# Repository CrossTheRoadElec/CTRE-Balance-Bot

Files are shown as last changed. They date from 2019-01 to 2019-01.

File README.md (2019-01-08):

# CTRE Balance Bot v2

## What's In Here
- STL files for printing the balance bot: **[CAD Files](CAD/)**
- Instructions on how to assemble the balance bot: **[Builders Guide](Documentation/)**
- Source code to get the balance bot balancing on its own

## What You Need
- 3D Printer or means of printing the required STL files
- Phoenix NETMF v5.1.5.0 (Found in Phoenix 5.6.0.0 found [here](http://www.ctr-electronics.com/installer-archive))
- The Balance Bot Kit sold from CTR Electronics at http://www.ctr-electronics.com/

## What This Is

Balance Bot

This is a demo robot that shows how PID can be used to control something inherently unstable (an inverted pendulum) in a very controllable manner.

This is done through various control schemes, that you can look at [here](#control-schemes)

## How To Make One
1. Assemble the hardware as shown in the **[Builders Guide](Documentation/)**.
2. Ensure Phoenix 5.6.0.0 is installed and Phoenix NETMF 5.1.5.0 is referenced in the solution explorer.

http://www.ctr-electronics.com/installer-archive

This can be confirmed below...

Assembly Version Reference

3. Flash all hardware using Phoenix Lifeboat.
    1. HERO firmware is 1.2.0.0
    2. Talon firmware is 11.8
    3. Pigeon firmware is 0.41
4. Deploy code to HERO.
5. Done!

## Controls
All the controls are configurable within the source code, you can change any button you want.
Default controls are:
- A - Re-Zero the balance bot to make its current pitch the 0 pitch
- X - Enable closed-loop control of the balance bot to attempt to balance on the surface
- Start - Enable *Pixy Control* mode
- Shift from D input to X input mode - Disable robot
- Shift from X input to D input mode - Enable robot
---
Gain Tuning Controls:
- RB - Increment currently selected gain by increment amount shown in yellow above gains
- LB - Decrement currently selected gain by increment amount shown in yellow above gains
- Back - Cycle increment amount between 0.001 -> 0.010 -> 0.100 -> 1.000 -> 10.00 -> 0.001
- B - Cycle currently selected gains by P -> I -> D -> P
- Y - Cycle currently selected gains by Top -> Mid -> Bottom -> Top

## Control Schemes
There are also various features available that allow for better control

- Cascaded PID Loop
  - (Pixy Camera PID) feeds desired velocity to maintain distance into a
  - Velocity Control PID feeds angle to maintain velocity into a 
  - Balance Control PID outputs percent output to maintain angle
  - The outer control loop (Velocity) runs at a slower rate than the inner loop (Balance) to ensure the balance loop has time to react to any velocity changes. This is key to ensuring the robot balances properly.
- Fall Detection
  - When the robot surpasses a specified angle for too long, it will have *tipped over*.
  - When *tipped over*, the robot must be uprighted for some time before it will be given control again and attempt to balance again.
  - The *tipped over* angle changes based on the velocity of the robot, if it's moving forward a great velocity, it is unable to accelerate in that direction for very much, so the fall detection recognizes it is unable to recover if angled in the direction of travel and determines it has *tipped over*
    - Likewise, if the robot is moving forward at a great velocity, it is able to angle against the direction of travel at a greater angle than normal due to it having more room to accelerate without having it *tipped over*.
 - Pixy Camera
    - Every robot has the ability to enable *Pixy Control* mode by pressing start on the gamepad.
    - *Pixy Control* is visible due to the screen having turned blue on the robot
    - If the robot has a Pixy Camera attached to it, it will actively look for blue objects with a similar luninence to the Display Module Screen
        - If it finds an object that matches what it's looking for, it will take control away from the user and attempt to face in its direction and maintain a distance such that the height of the target matches a predefined height in the code.
    - If there is no Pixy Camera attached to a robot with *Pixy Control* active, it will just have the blue screen on and have full user control, other robots will still be able to follow it.
- Low Battery Voltage Detection
    - Once the battery is measuerd to be less than what the robot expects a battery voltage to be at (currently set to 11.00V), the robot will enter *Low Battery* mode.
    - While in *Low Battery* mode, the robot will feel sluggish and the display will show a red background if not in *Pixy Control* mode.
    - Once the robot is in *Low Battery* mode, it will not exit until the voltage reaches a good voltage (currently 11.50V). This is to ensure the robot does switch between *Low Battery* and good battery due to motor loads.
    - This feature is to ensure the battery does not discharge below a certain point, and to let the user know the battery is low so they can charge it.

## What's the screen for?
The screen is used for debugging purposes, when dialing in gains it's useful to be able to change the gains on the fly to test various gains without having to re deploy the application.

It also displays the current pitch the robot is at, along with the battery voltage it is measuring, whether closed looping is enabled or not, and what the percent output to the motors are at. All of this is useful for debugging various issues with the robot.

Lastly, there are points on the screen, normally 'o's. They show what direction each wheel of the robot is traveling in. This is useful as it allows the builder to double check they did the wiring correctly. If the robot is pushed forward such that the wheels turn, both of the displays should show up as a '+'. If just one wheel is pushed forward, only that side should show up as a '+'. Likewise for going backwards, they should show up as a '|' or when viewed directly at it a '-'.

Besides this, it will turn blue when the robot is in *Pixy Control* mode, this allows other pixy cameras to detetct where the robot is and attempt to face towards the blue-screened robot and maintain a distance away from the robot.

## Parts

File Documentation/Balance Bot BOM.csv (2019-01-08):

Subteam | Part | Part Number | Quantity | Link | Details
Drivetrain(pololu) | 30:1 37D metal gearmotor | 2823 | 2 | https://www.pololu.com/product/2823
 | 6mm D hub | 1083 | 1 | https://www.pololu.com/product/1083 | 2 - pack
 | 6mm D hub (alt) | RB-Sct-1045 | 2 | https://www.robotshop.com/en/6mm-clamping-d-hub-tapped-0770-pattern.html
 | Traction Tire | 217-2859 | 1 | https://www.vexrobotics.com/vexpro/motion/wheels-and-hubs/traction-wheels.html | 2 - pack
Control System | Talon SRX | 14-838288 | 2 | http://www.ctr-electronics.com/talon-srx.html
 | HERO Dev board | 16-728279 | 1 | http://www.ctr-electronics.com/hro.html
 | Pigeon IMU | 16-737785 | 1 | http://www.ctr-electronics.com/gadgeteer-imu-module-pigeon.html
 | Display Module | 16-688380 | 1 | http://www.ctr-electronics.com/gadgeteer-display-module.html | Cable Included
 | CAN Connector | 15-676778 | 1 | http://www.ctr-electronics.com/can-connector-5-pack.html
 | Ribbon Cable | 14-886867 | 1 | http://www.ctr-electronics.com/talon-srx-data-cable-4-pack.html
 | Power Breakout PCB | 17-806679 | 1 | http://www.ctr-electronics.com/power-distribution-breakout.html
 | Talon SRX Encoder Breakout Board | 15-696679 | 2 | http://www.ctr-electronics.com/talon-srx-encoder-breakout-board.html
 | Battery | 522-1009-ND | 1 | https://www.digikey.com/product-detail/en/b-b-battery/BP3-12-T1/522-1009-ND/653330
 | Battery Charger |  | 1 | https://www.amazon.com/Energizer-ENC2A-Battery-Charger-Maintainer/dp/B01GSI1S08?s=automotive
 | Velcro |  | 1 | https://www.amazon.com/Monoprice-Hook-Loop-Fastening-0-75-inch/dp/B004AF9II6
 | Fuse holder | 8110K4 | 1 | https://www.mcmaster.com/#8110k4/=1dkxrrj
 | Fuse | F4201-ND | 1 | https://www.digikey.com/product-detail/en/littelfuse-inc/0287020.PXCN/F4201-ND/2519821 | Same fuse as PDP hardware kit
 | Black Anderson housing | 17-808066 | 6 | http://www.ctr-electronics.com/anderson-power-pole-44.html | Battery to Power & Motors to Talons
 | Red Anderson housing | 17-808082 | 6 | http://www.ctr-electronics.com/anderson-power-pole.html | Battery to Power & Motors to Talons
 | Yellow Anderson housing | 17-808089 | 1 | http://www.ctr-electronics.com/anderson-power-pole-46.html | CAN Diagnostic port
 | Green Anderson housing | 17-808071 | 1 | http://www.ctr-electronics.com/anderson-power-pole-45.html | CAN Diagnostic port
 | PP15 crimp | 879-1332 | 6 | http://www.ctr-electronics.com/anderson-power-pole-contact-42.html | Motor Power & CAN port
 | PP45 crimp | 879-261G2 | 8 | http://www.ctr-electronics.com/anderson-power-pole-contact-43.html | Talons & Battery & Power
 | 12AWG silicon wire RED | 15-838782 | 5 | http://www.ctr-electronics.com/red-silicone-wire-12-awg.html
 | 12AWG silicon wire BLACK | 15-838766 | 5 | http://www.ctr-electronics.com/black-silcone-wire-12-awg.html
 | Orange 20 awg furrle | 15-705048 | 1 | http://www.ctr-electronics.com/ferrule-20-awg.html
 | White 18 awg furrle | 15-704956 | 1 | http://www.ctr-electronics.com/ferrule-18-awg.html
 | USB A to mini male B | 16-856566 | 1 | http://www.ctr-electronics.com/usb-a-male-b-mini-cable.html
 | USB A to A | 16-856565 | 1 | http://www.ctr-electronics.com/usb-a-male-cable.html
Hardware | 4-40 .25"(1/4) legnth SH | 92196A106 | 1 | https://www.mcmaster.com/#92196a106/=1dlje7x | 10 Total
 | 4-40 .5"(1/2) length SH | 92196A110 | 1 | https://www.mcmaster.com/#92196a110/=1dljeei | 70 Total
 | 4-40 nylock hex nut | 91831A005 | 1 | https://www.mcmaster.com/#91831a005/=1dljdbn | 28 Total
 | #4 washer | 92141A005 | 1 | https://www.mcmaster.com/#92141a005/=1dlkrwv | 30 Total
 | 8-32 1" length | 92196A199 | 1 | https://www.mcmaster.com/#92196a199/=1dljfxc | 4 Total
 | M3 6mm length SH | 91502A102 | 1 | https://www.mcmaster.com/#91502a102/=1dljgex | 12 Total
Tools | #43 Drill | 2901A217 | 1 | https://www.mcmaster.com/#2901a217/=1dytp8s
 | 1/8" Drill | 2901A115 | 1 | https://www.mcmaster.com/#2901a115/=1dytt2i
 | #25 Drill | 2901A198 | 1 | https://www.mcmaster.com/#2901a198/=1dytth4
 | 4-40 Tap | 2522A665 | 1 | https://www.mcmaster.com/#2522a665/=1dytw9t
 | Locktite | 1004A12 | 1 | https://www.mcmaster.com/#1004a12/=1e2fvdl

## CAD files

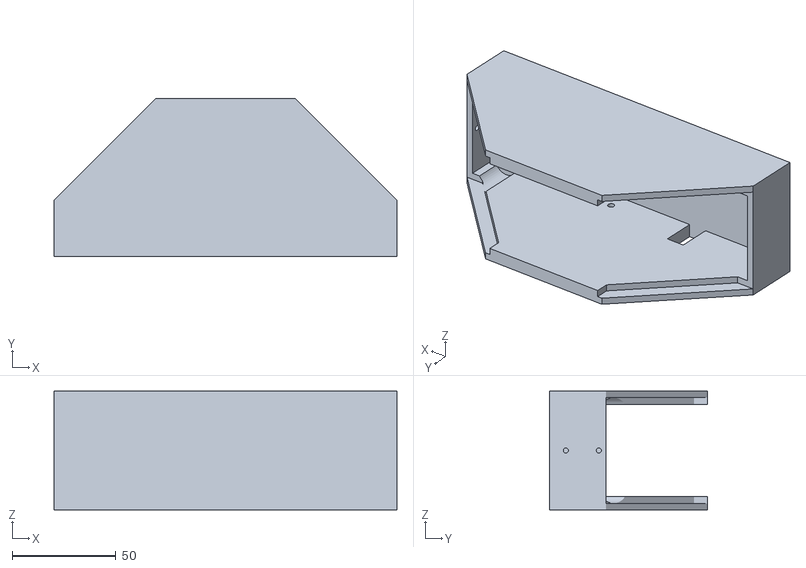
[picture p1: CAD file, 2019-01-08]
CAD/Dock Assm - Dock Corner-1.STL
165.1 x 76.2 x 57.1

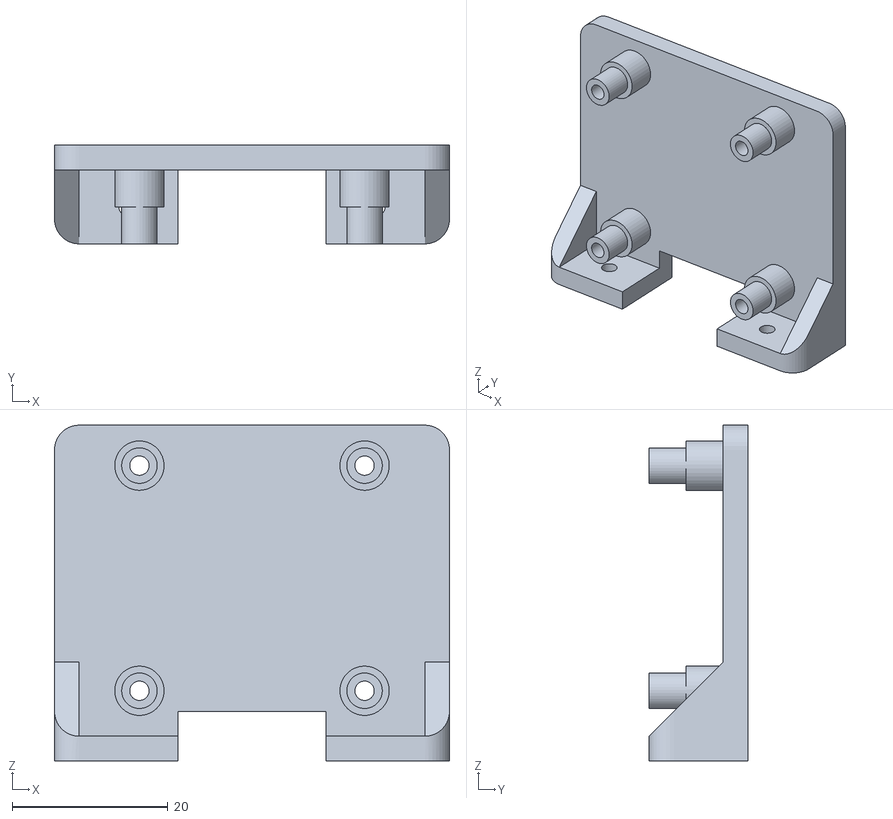
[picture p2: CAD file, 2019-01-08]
CAD/Pigeon Mount.STL
50.8 x 12.7 x 43.2

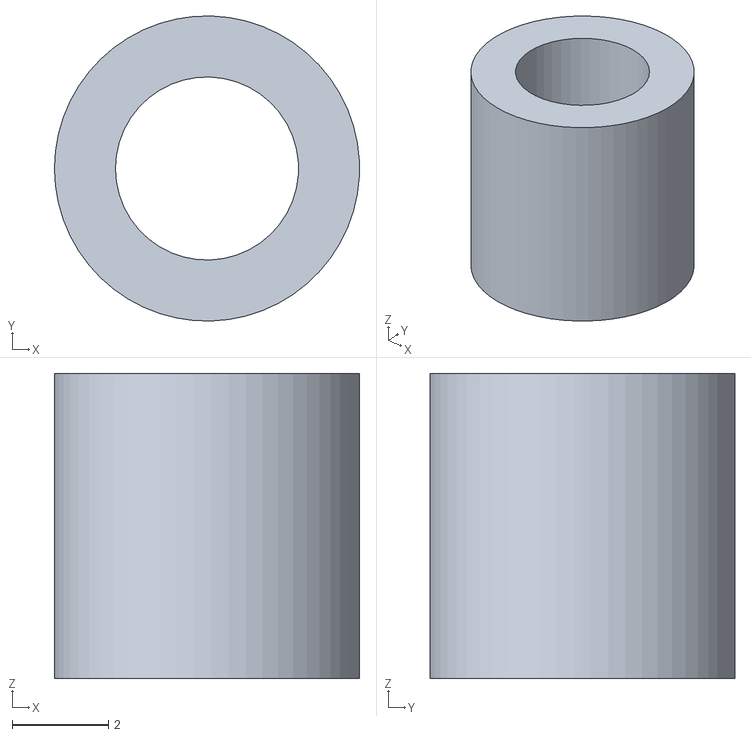
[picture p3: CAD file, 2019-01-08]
CAD/Spacer.STL
6.35 x 6.35 x 6.35

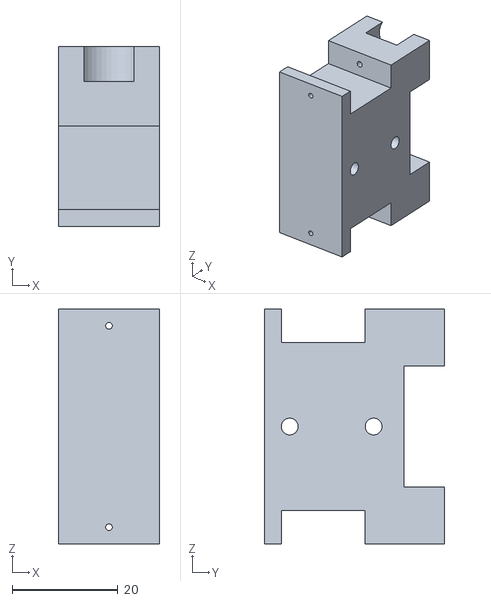
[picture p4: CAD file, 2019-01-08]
CAD/Dock Assm - Pogo Clamp-1.STL
19.1 x 34.0 x 44.4

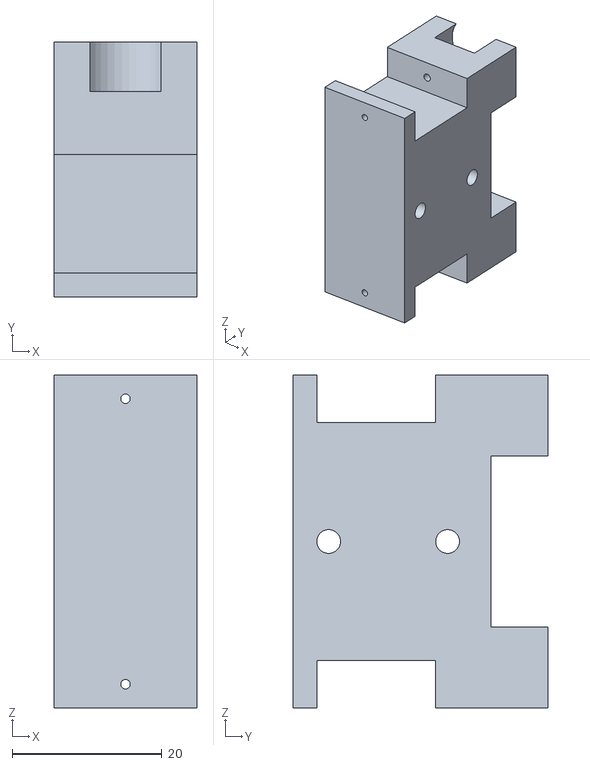
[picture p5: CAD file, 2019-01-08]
CAD/Pogo Clamp.STL
19.1 x 34.0 x 44.5

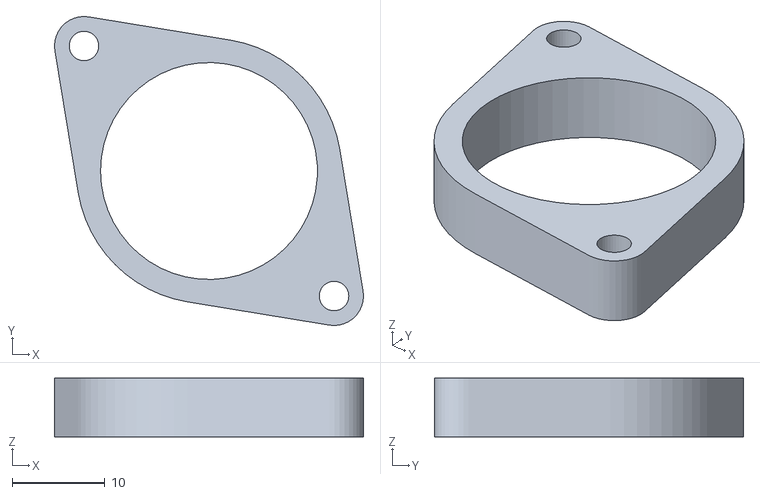
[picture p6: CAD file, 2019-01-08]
CAD/Switch Cover.STL
33.3 x 33.3 x 6.35

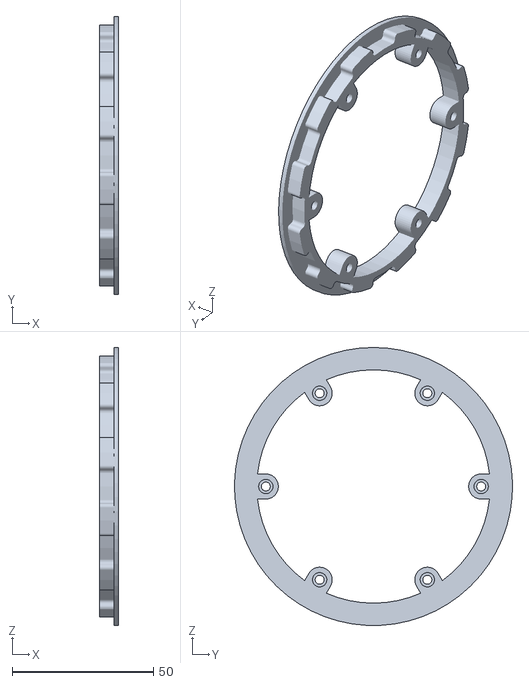
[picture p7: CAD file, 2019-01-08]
CAD/4in Traction flange.STL
6.67 x 98.4 x 98.4

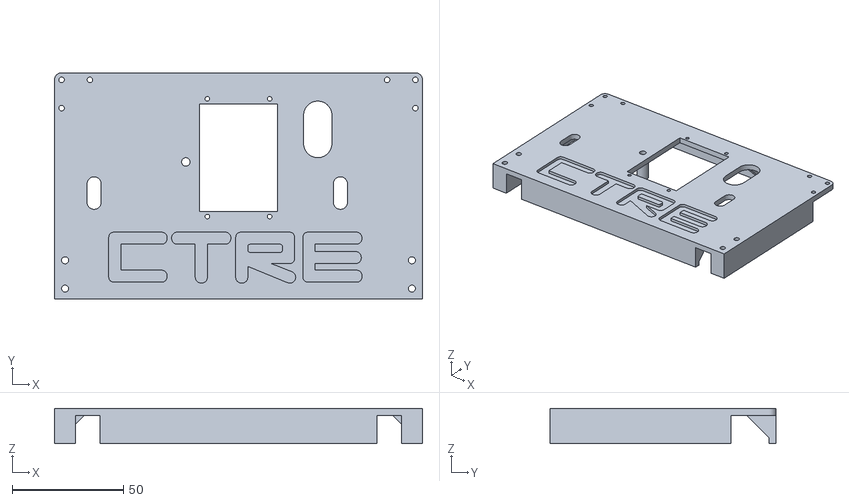
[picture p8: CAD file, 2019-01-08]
CAD/Front Cover V2.STL
165.1 x 101.6 x 15.9

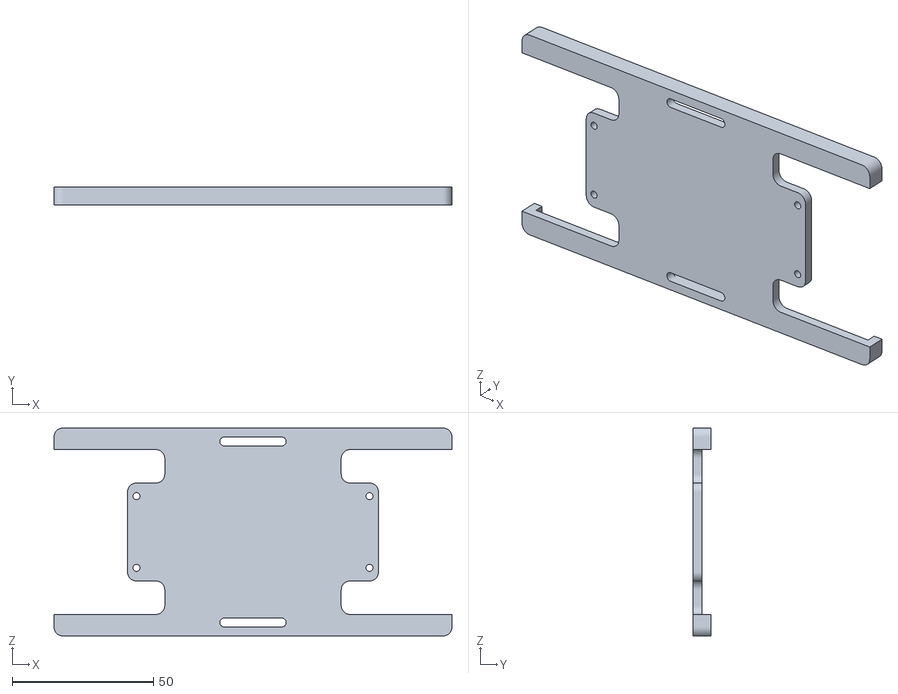
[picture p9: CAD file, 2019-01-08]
CAD/Cross beam.STL
141.0 x 6.35 x 73.7

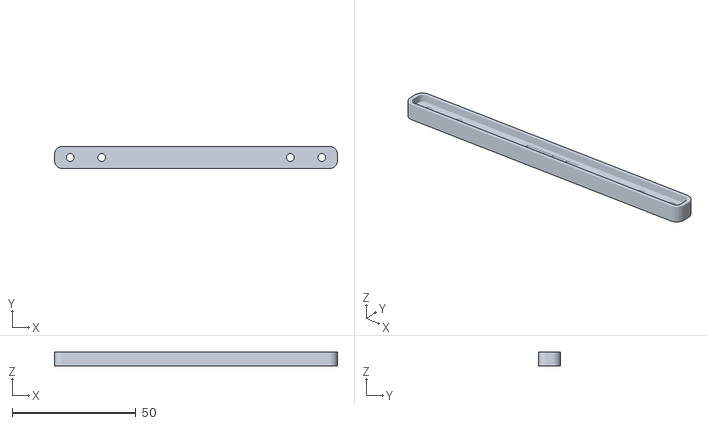
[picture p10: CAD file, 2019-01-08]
CAD/Front Support.STL
114.3 x 8.89 x 5.72

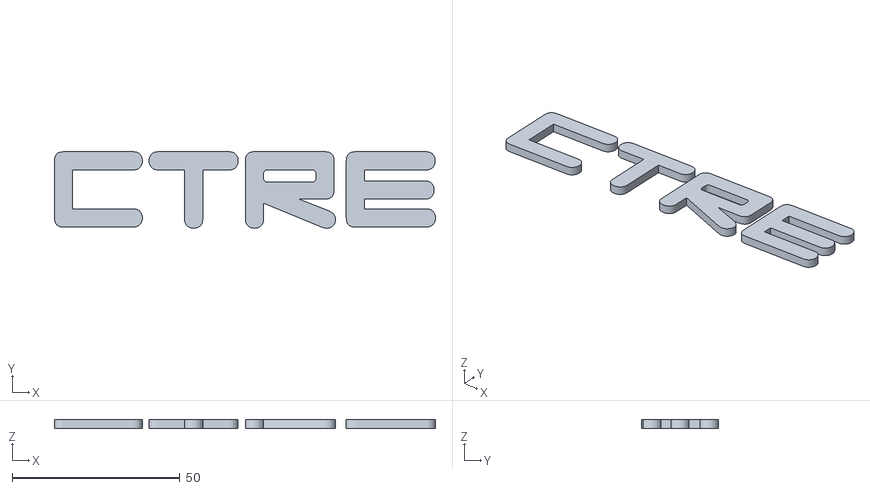
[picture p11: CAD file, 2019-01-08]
CAD/CTRE lettering.STL
113.7 x 22.9 x 2.54

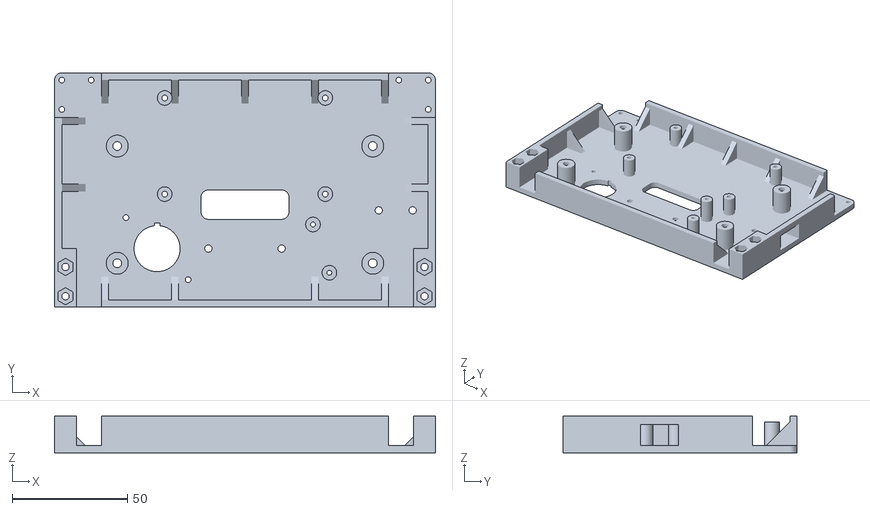
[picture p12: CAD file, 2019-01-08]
CAD/Back Cover V2.STL
165.1 x 101.6 x 15.9

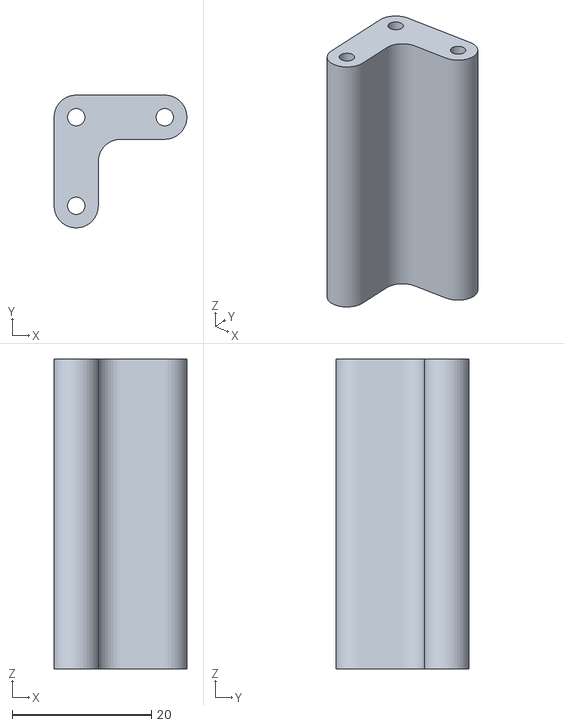
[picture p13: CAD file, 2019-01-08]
CAD/Corner Support.STL
19.1 x 19.1 x 44.5

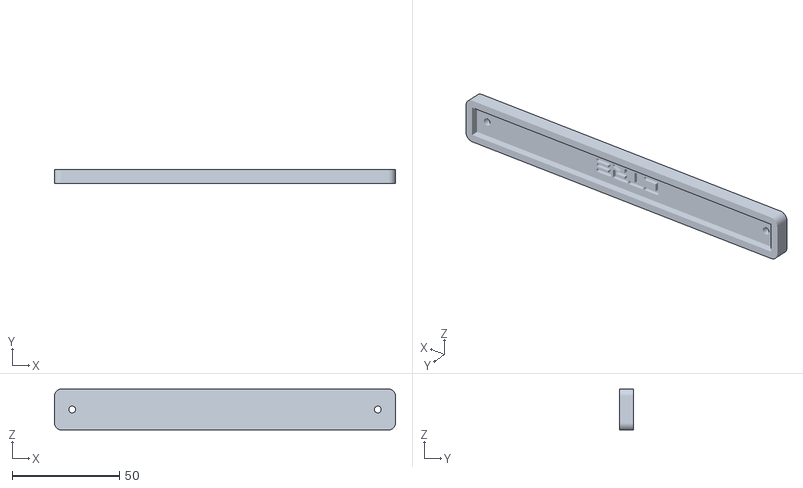
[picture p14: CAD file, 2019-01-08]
CAD/Bottom Support.STL
158.8 x 6.35 x 19.1

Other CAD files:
CAD/CTRE 4in Traction flange.STL
CAD/Dock Corner.STL
CAD/Side Support.STL
CAD/4in Traction hub V2.STL
CAD/4in Traction hub.STL
CAD/Motor mount.STL

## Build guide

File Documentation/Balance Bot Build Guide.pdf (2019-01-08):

# Balance Bot Build Guide

## Table of Contents

# Introduction

Purpose: To provide an economic robotic platform that utilizes many CTRE control system products for programming entertainment, while being cheap and easy to manufacture with just a 3D printer and hand tools.

Port layout:

- USB Mini is accessible from the top of the robot.

Tools:
- Drill Bits
- #43 (#4 Tap)
- ⅛ (#4 through hole)
- #25 (#8 tap)
- Allen wrenches (recommended : Harbor Freight (https://www.harborfreight.com/10-Pc-SAE-T-Handle-Hex-Key-Set-62161.html) )
- 3/32 (#4 socket head bolt)
- 9/64 (#8 Socket head bolt)
- Needle Nose Pliers
- Electrical
- Wire strippers
- Ferrule Crimper (http://www.ctr-electronics.com/weidmuller-ferrule-crimper.html)
- Anderson Crimper (http://www.ctr-electronics.com/anderson-powerpole-crimper-crimp.html)
- Snips
Material:
- .9lbs PLA Filament

# Printing Parts

## 1. Print a Back Cover

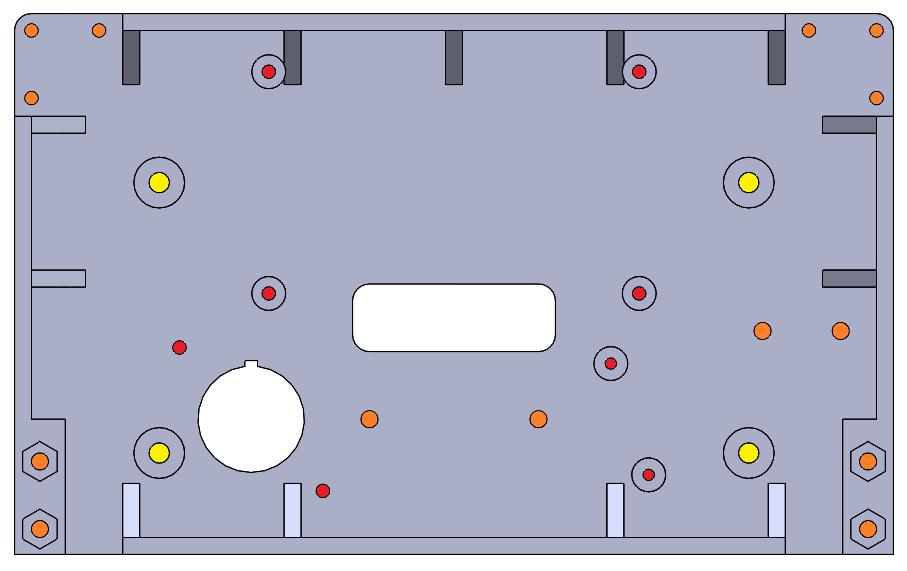
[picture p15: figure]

a. Drill RED holes with #43 drill
b. Drill ORANGE holes with ⅛ drill
c. Drill YELLOW holes with #25 drill

d. Press #4 lock nuts into hex

## 2. Print a Front Cover

a. Drill RED holes with #43 drill

b. Drill ORANGE holes with ⅛ drill
c. Drill YELLOW holes with #25 drill

## 3. Press in #4 Nuts into hex grove

*make sure the nylon on the nut is facing the correct direction

## 4. Print two Motor Mounts

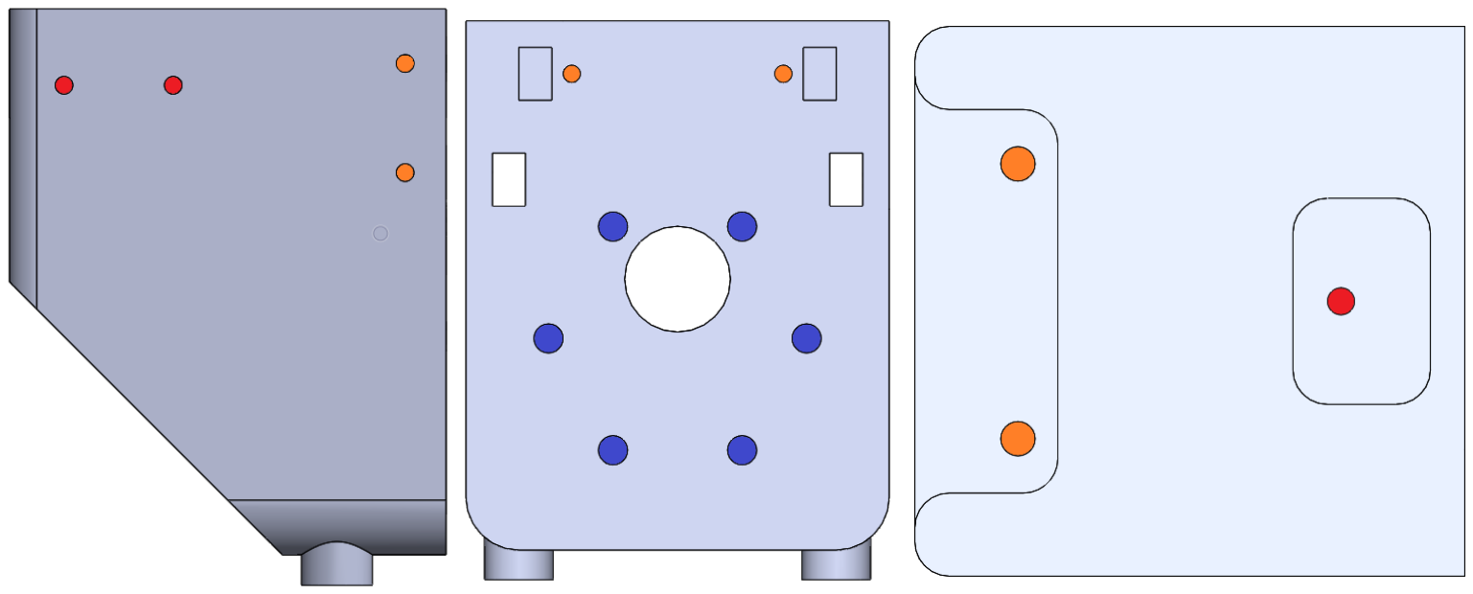
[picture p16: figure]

a. Drill RED holes with #43 drill
b. Drill ORANGE holes with ⅛ drill
c. Blue holes are for M4 bolts

## 5. Print two Side Supports

a. Drill out ORANGE holes with ⅛ drill

## 6. Print a Cross Beam

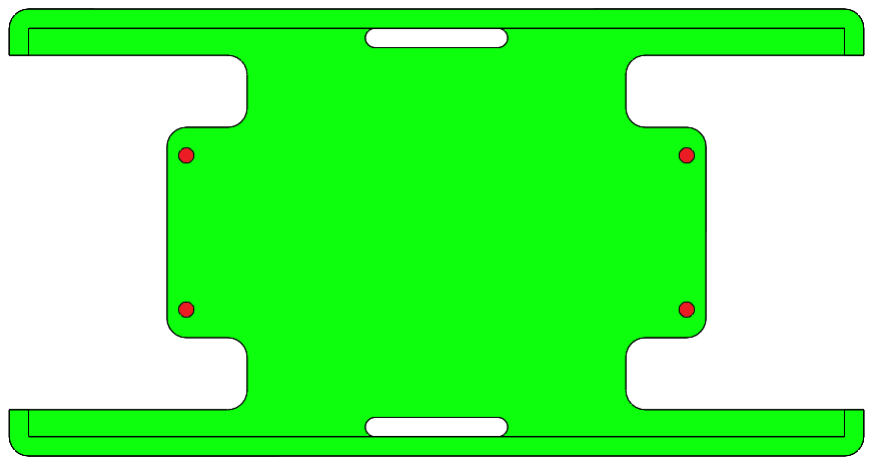
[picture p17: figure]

a. Drill RED holes with a #43 drill

## 7. Print a Pigeon Mount

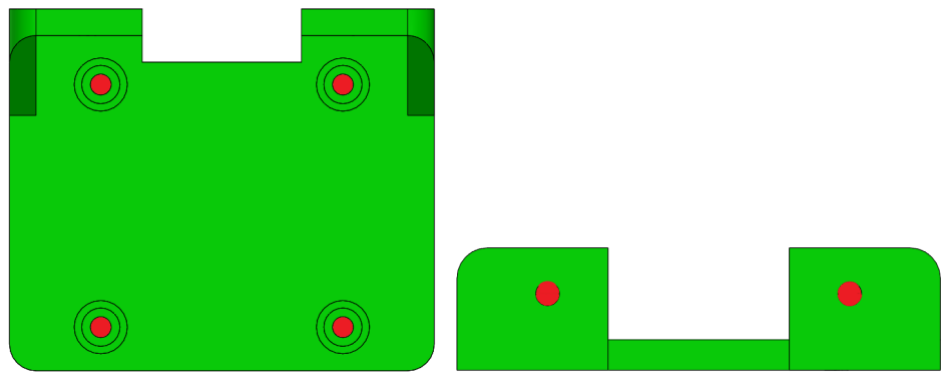
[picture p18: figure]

a. Drill RED holes with #43 drill

## 8. Print two Corner Supports

a. Drill RED holes with a #43 drill on both sides

## 9. Print two Front Supports

a. Drill ORANGE holes with ⅛ drill

## 10. Print two 4in Traction Hub

a. Drill ORANGE holes with ⅛ drill

b. Press in #4 nuts into hex groove

## 11. Print two 4in Traction Flange

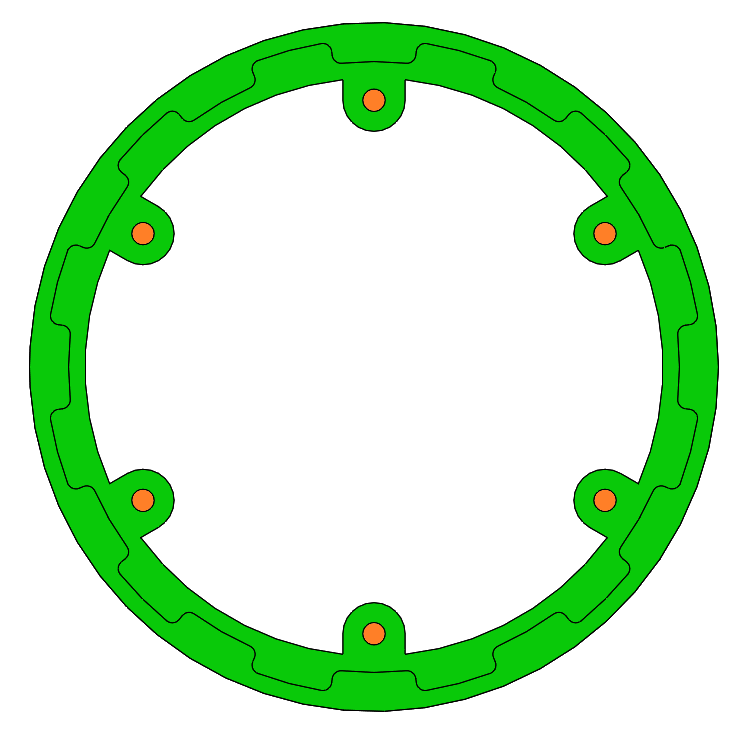
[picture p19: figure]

a. Drill ORANGE holes with ⅛ drill

## 12. Print four spacer

# Assembly

## 1. Assemble Wheel

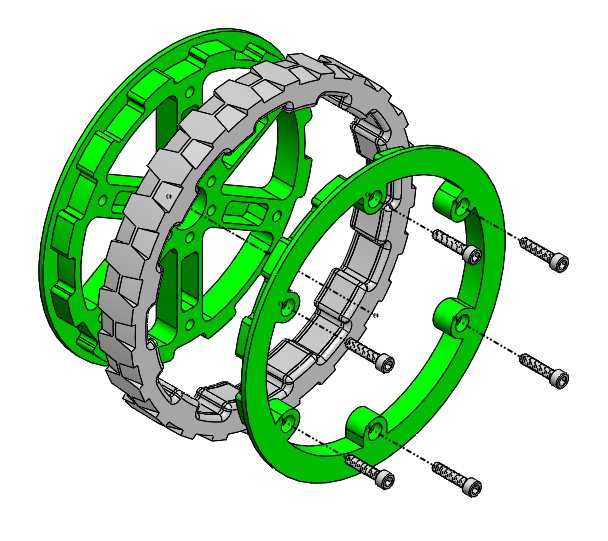
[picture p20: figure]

a. Sandwich the Traction wheel between the Hub and Flange, Secure with .5” 4-40 bolts

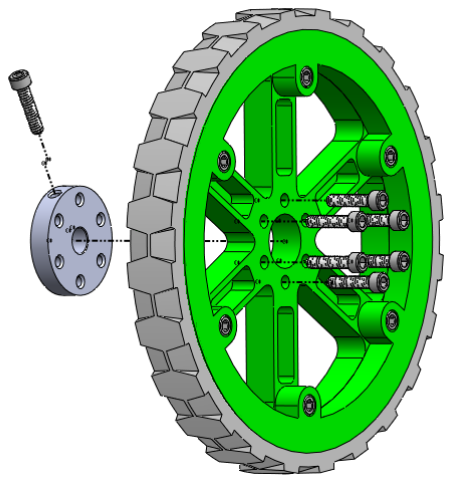
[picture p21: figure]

b. Attach the Pololu Mounting Hub to the Hub using .5” 4-40 bolts
c. Insert an additional .5” 4-40 into the Pololu Mount Hub to use as a set screw

## 2. Assemble Lower Frame

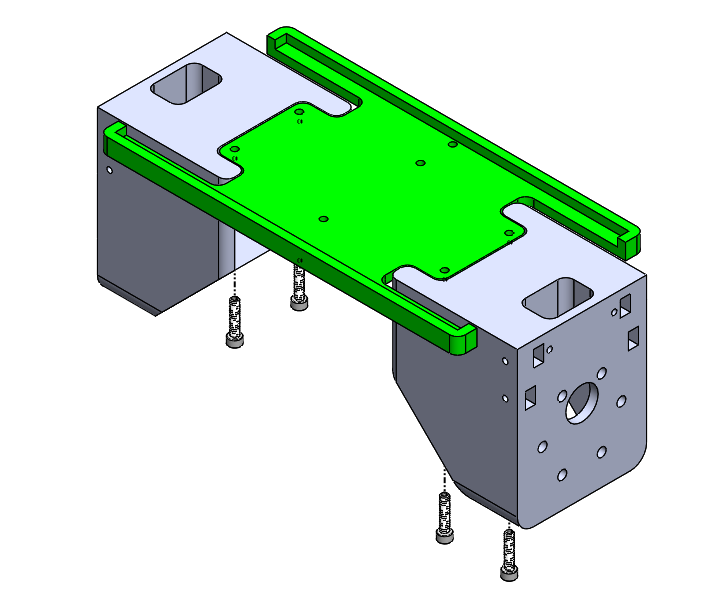
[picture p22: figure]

a. Attach the Motor Mounts to the Cross Beam using .5” 4-40 bolts

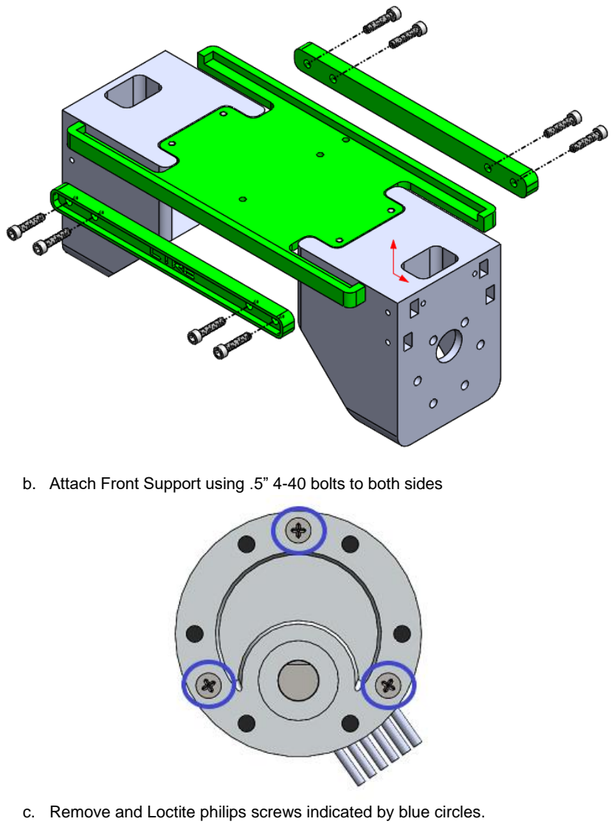
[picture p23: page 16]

b. Attach Front Support using .5” 4-40 bolts to both sides
c. Remove and Loctite philips screws indicated by blue circles.

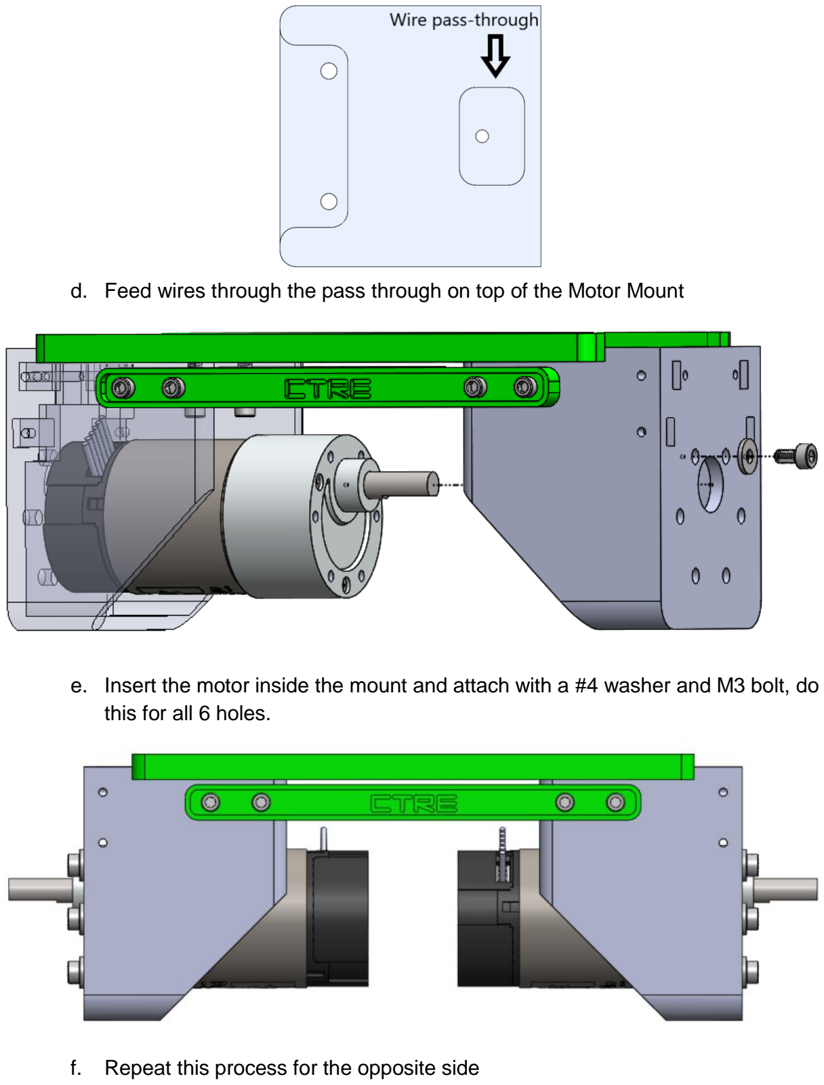
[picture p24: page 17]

d. Feed wires through the pass through on top of the Motor Mount
e. Insert the motor inside the mount and attach with a #4 washer and M3 bolt, do this for all 6 holes.
f. Repeat this process for the opposite side

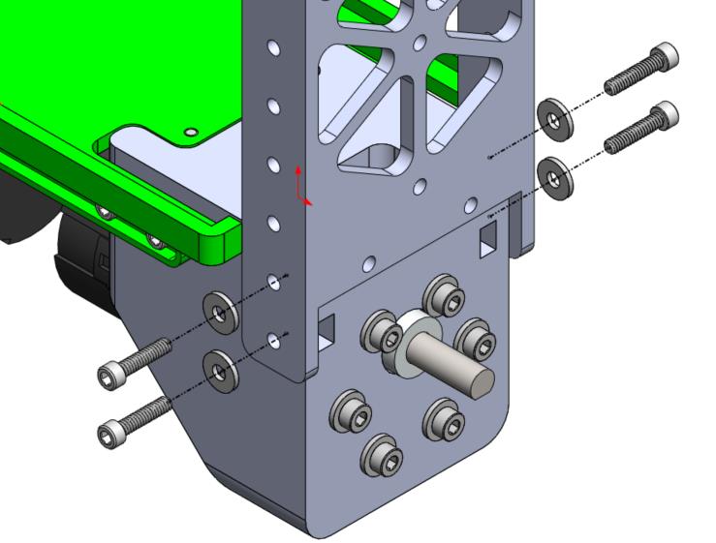
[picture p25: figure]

g. Attach the Side Supports using #4 washers and .5” 4-40 bolts(with nuts already installed)

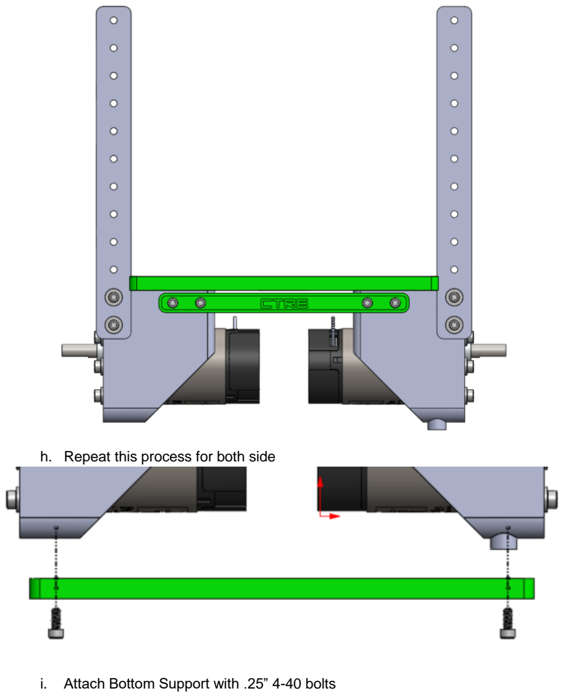
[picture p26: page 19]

h. Repeat this process for both side
i. Attach Bottom Support with .25” 4-40 bolts

## 3. Assemble Back Cover

a. Attach Corner Support with .5” 4-40 bolts Wire Electronics
Power Wiring Diagram

# Signal Wiring Diagram

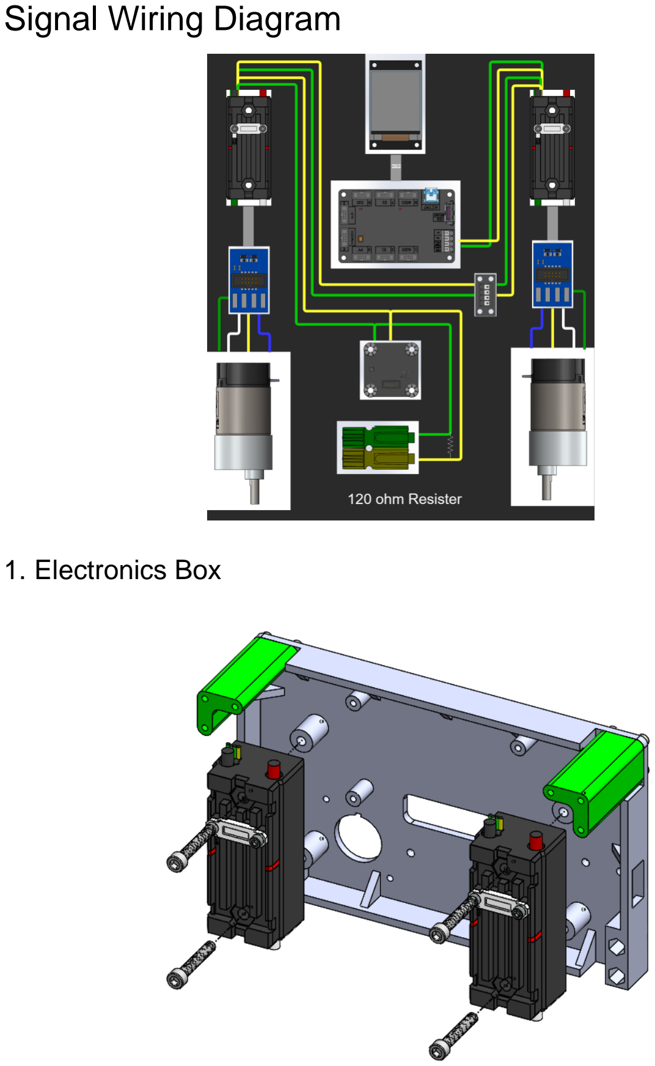
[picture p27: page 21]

## 1. Electronics Box

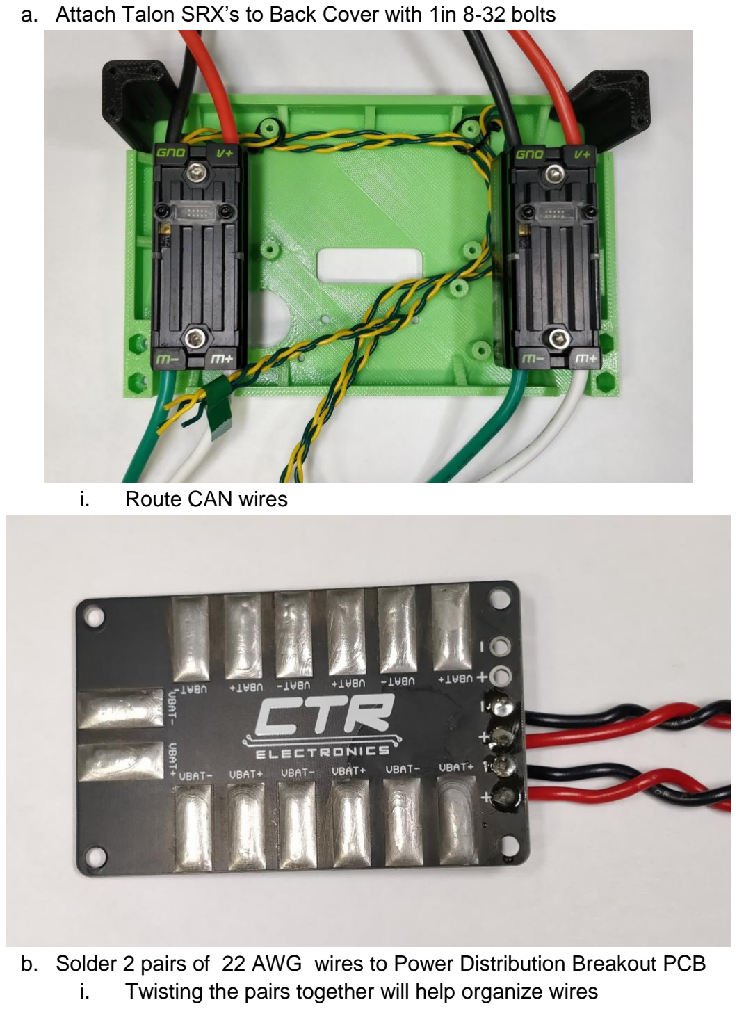
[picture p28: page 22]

a. Attach Talon SRX’s to Back Cover with 1in 8-32 bolts
i. Route CAN wires
b. Solder 2 pairs of 22 AWG wires to Power Distribution Breakout PCB
i. Twisting the pairs together will help organize wires

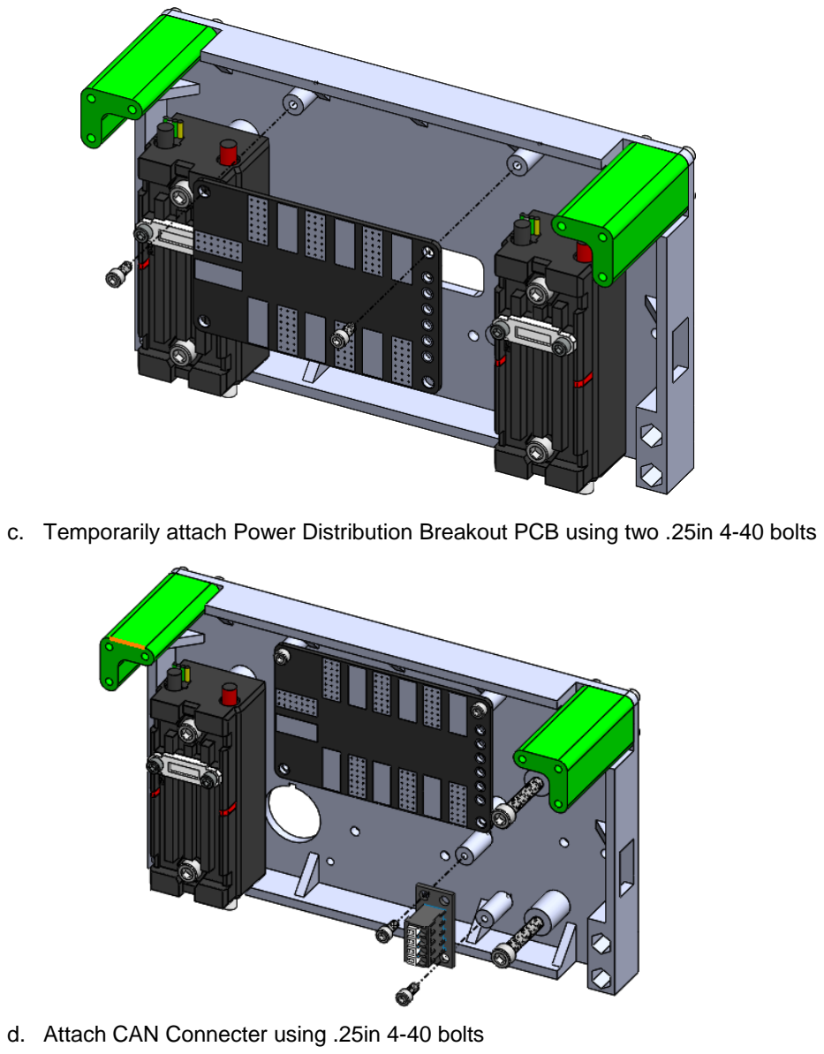
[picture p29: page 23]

c. Temporarily attach Power Distribution Breakout PCB using two .25in 4-40 bolts
d. Attach CAN Connecter using .25in 4-40 bolts

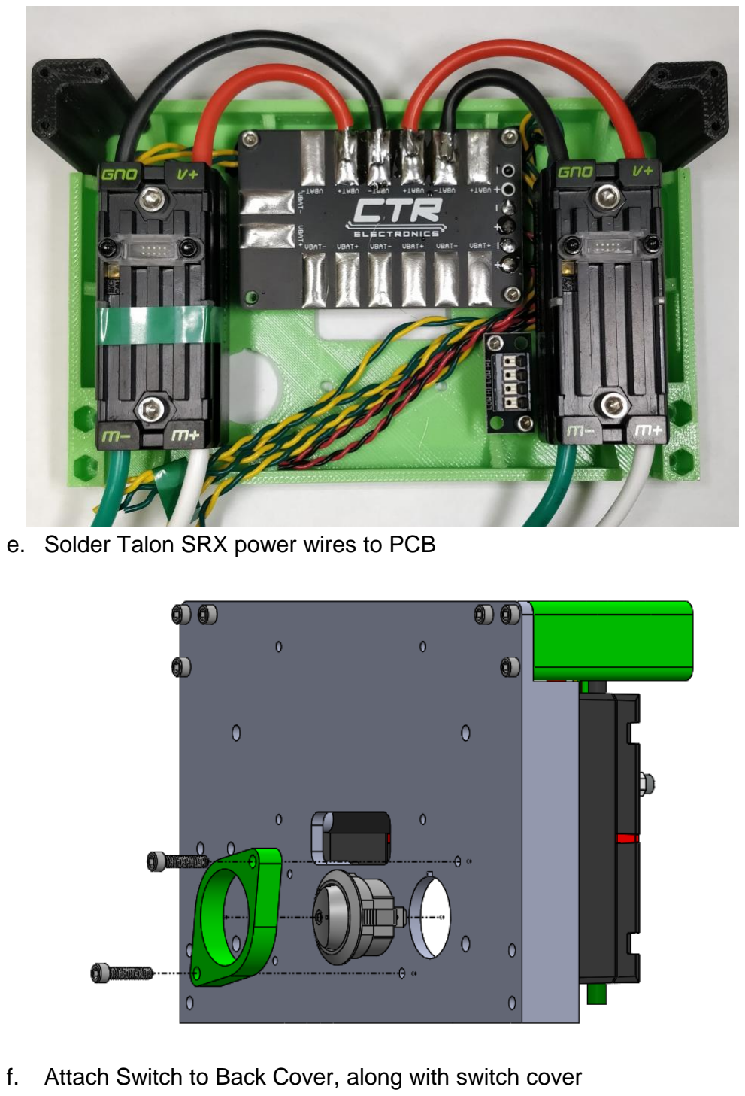
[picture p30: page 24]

e. Solder Talon SRX power wires to PCB
f. Attach Switch to Back Cover, along with switch cover

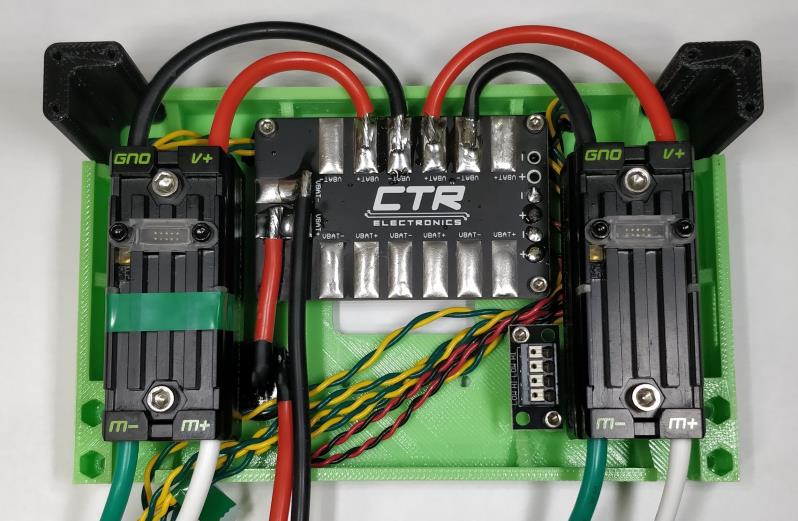
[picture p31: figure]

g. Solder 12 AWG wire from the Switch to the PCB and route battery cable and attach Andersons
h. Take out the two temporary .25in 4-40 bolts

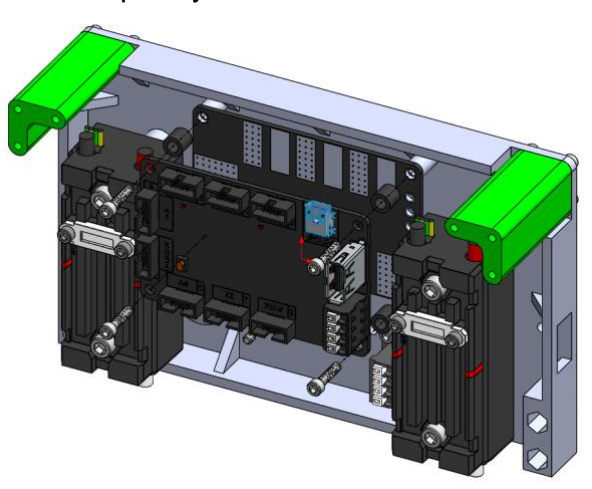
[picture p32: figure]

i. Attach the HERO Development board using .5in Spacers and .5in 4-40 bolt
j. Use Ferrules to plug in CAN to HERO and CAN Connector. Along with with Power to HERO

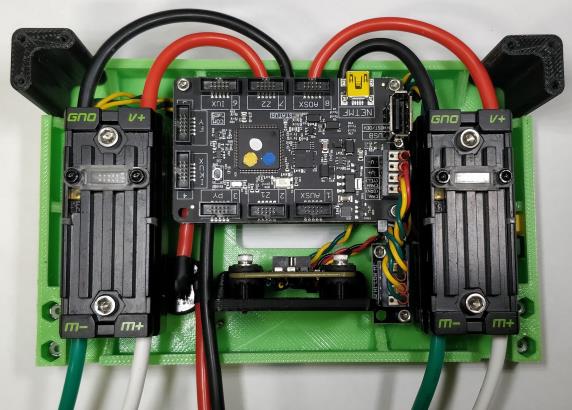
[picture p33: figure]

k. Solder power and CAN wires to Pigeon and mount Pigeon

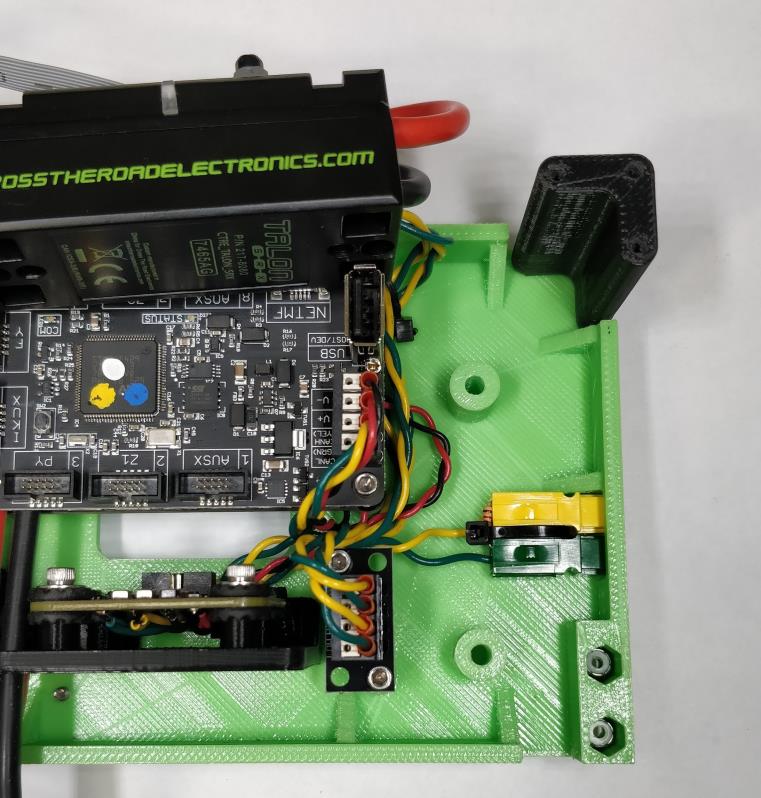
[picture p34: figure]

l. Anderson CAN
i. Optional 120 Ohm resistor with Anderson

# Final Assembly

## 1. Assemble Upper frame

a. Attach Display to Front Cover with .25in 4-40 bolts
i. Plug in display module using a 4in Gadgeteer Data Cable

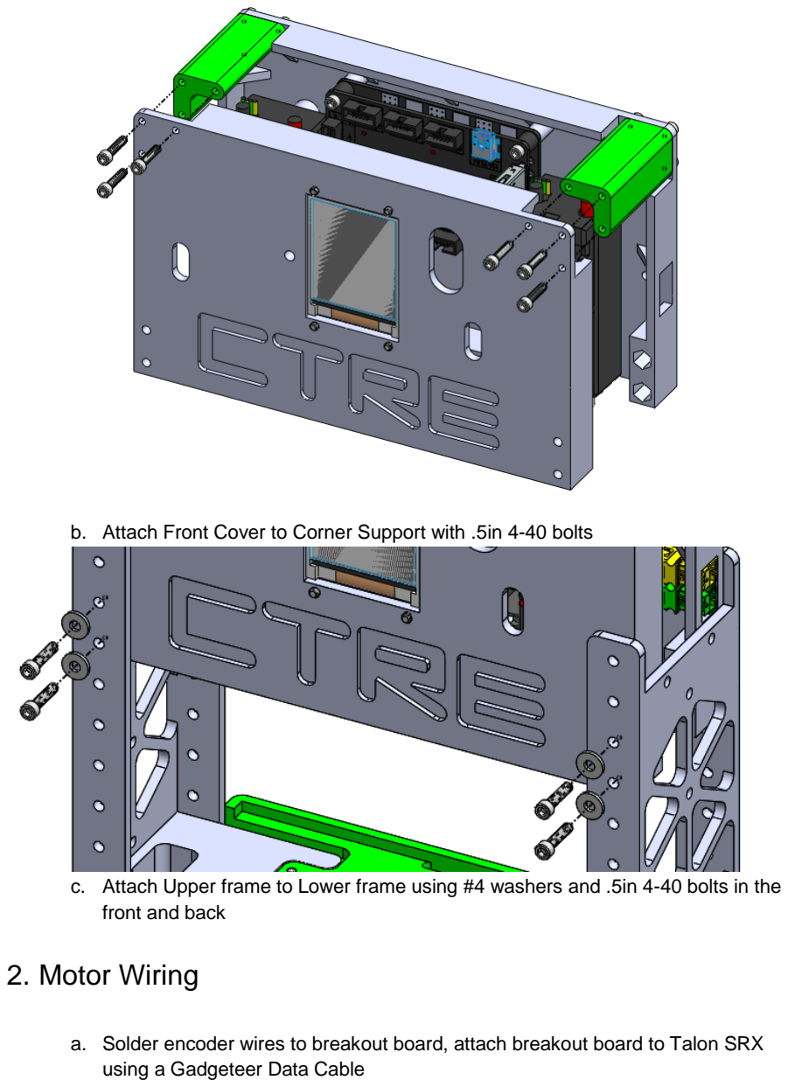
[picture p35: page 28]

b. Attach Front Cover to Corner Support with .5in 4-40 bolts
c. Attach Upper frame to Lower frame using #4 washers and .5in 4-40 bolts in the front and back

## 2. Motor Wiring

a. Solder encoder wires to breakout board, attach breakout board to Talon SRX using a Gadgeteer Data Cable

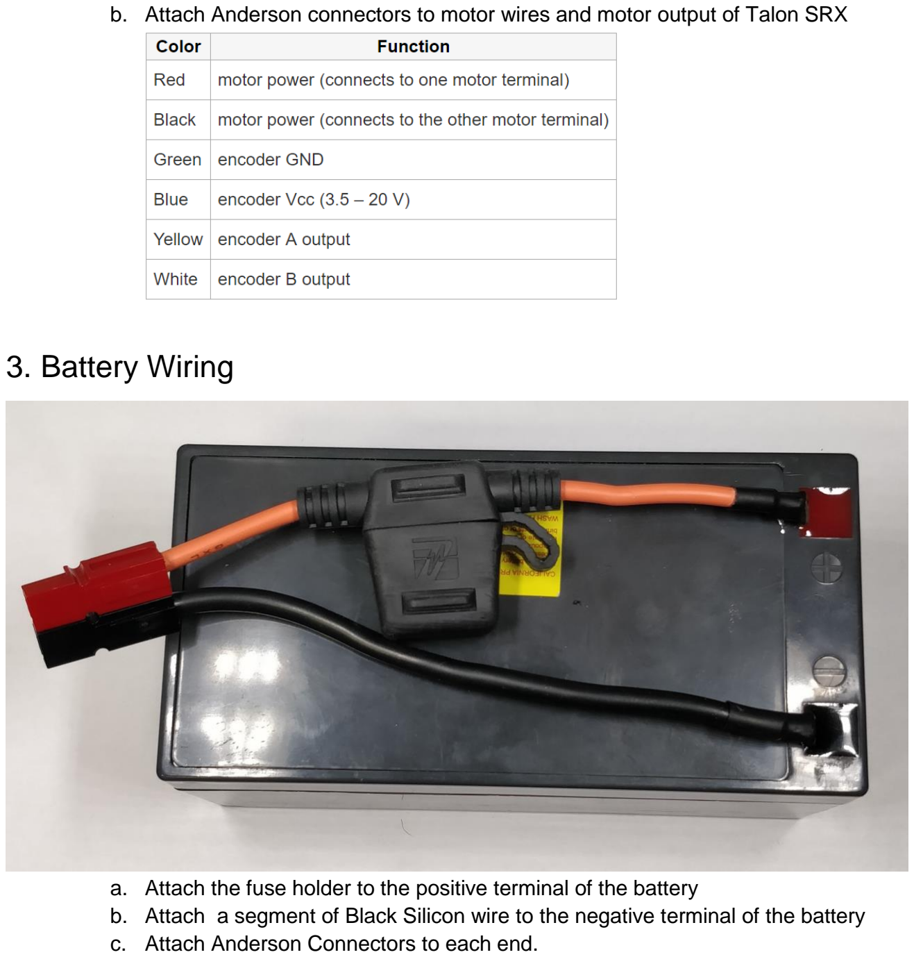
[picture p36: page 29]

b. Attach Anderson connectors to motor wires and motor output of Talon SRX

## 3. Battery Wiring

a. Attach the fuse holder to the positive terminal of the battery
b. Attach a segment of Black Silicon wire to the negative terminal of the battery
c. Attach Anderson Connectors to each end.

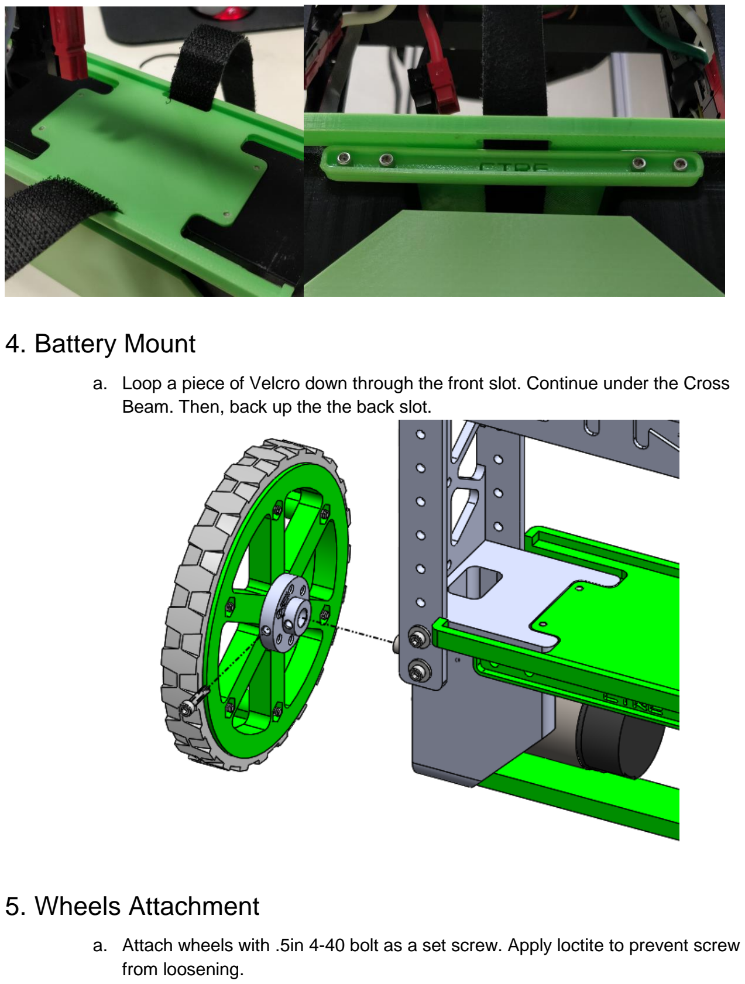
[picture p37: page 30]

## 4. Battery Mount

a. Loop a piece of Velcro down through the front slot. Continue under the Cross Beam. Then, back up the the back slot.

## 5. Wheels Attachment

a. Attach wheels with .5in 4-40 bolt as a set screw. Apply loctite to prevent screw from loosening.

# Optional Hardware

## 1. Dock

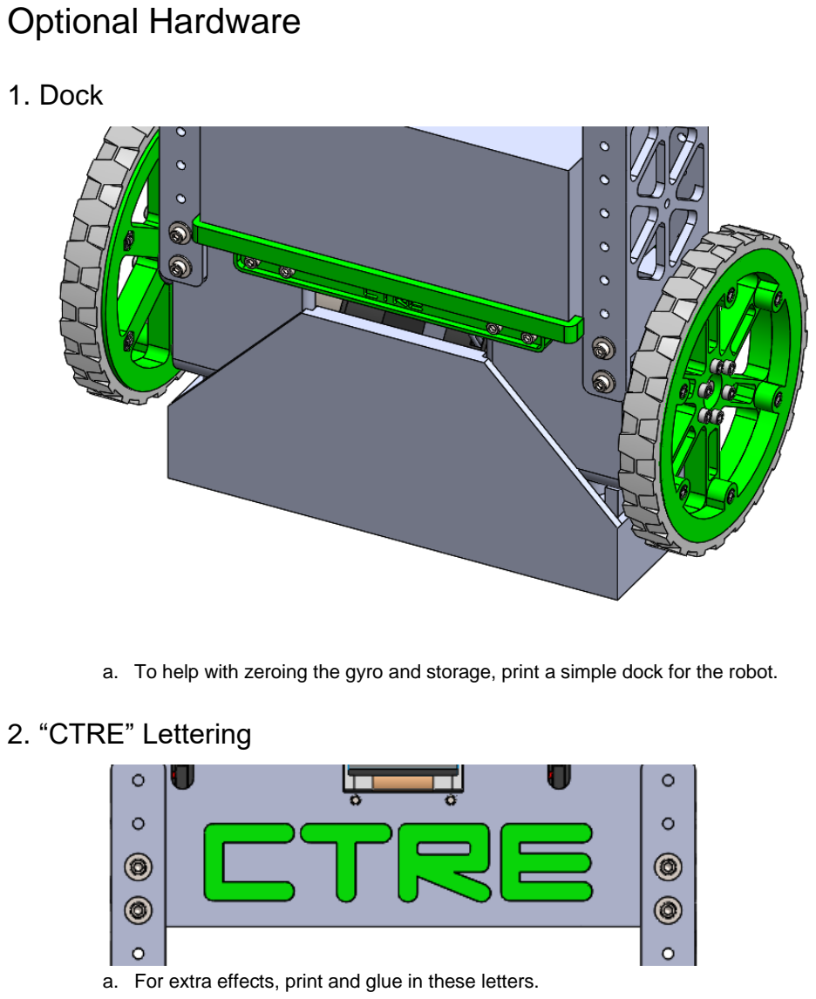
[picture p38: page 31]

a. To help with zeroing the gyro and storage, print a simple dock for the robot.

## 2. “CTRE” Lettering

a. For extra effects, print and glue in these letters.

# Revisions

Rev | Date | Description
1.0 | 18-Aug-2018 | First Release of document
